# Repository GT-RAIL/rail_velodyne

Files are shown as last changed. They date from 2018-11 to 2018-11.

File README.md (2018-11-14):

# RAIL Velodyne

This rail_velodyne repository includes custom packages required to install, simulate, and use the Velodyne VLP-16 with the Fetch. The drivers which bring up the physical VLP-16 were forked from [here](https://github.com/ros-drivers/velodyne) while the customized launch files to start the Fetch simluations that include the VLP-16 reuse models from [here](https://bitbucket.org/DataspeedInc/velodyne_simulator).

# Dependencies
Fetch packages for simulation. Please see [their site](http://docs.fetchrobotics.com/index.html) for installation instructions.

## Menu
1. [3D printed Mounts](#3d-printed-mounts) Go here to view the mounts for the VLP-16 and battery on Fetch.
2. [Fetch with Velodyne in Simulation](#fetch-with-velodyne-in-simulation) Go here for simulation install.
3. [Fetch with Velodyne on physical hardware](#fetch-with-velodyne-on-physical-hardware) Go here for robot install.
4. [Toggle the Velodyne on the Fetch](#toggle-the-velodyne-on-the-fetch) Go here to enable/disable Velodyne on robot.

## 3D printed Mounts
Mounts for VLP-16 and battery are found in [here](https://github.com/adaruna3/rail_velodyne/tree/master/fetch_velodyne/hardware). Some images of these mounts are below:

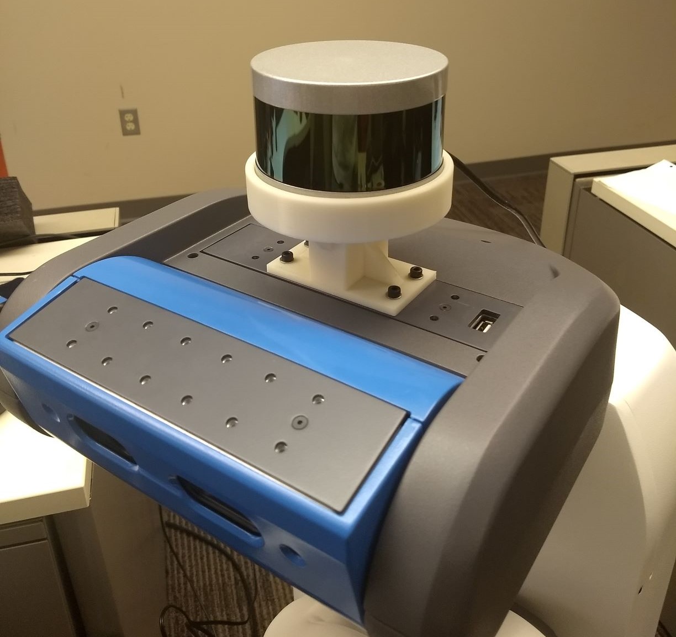
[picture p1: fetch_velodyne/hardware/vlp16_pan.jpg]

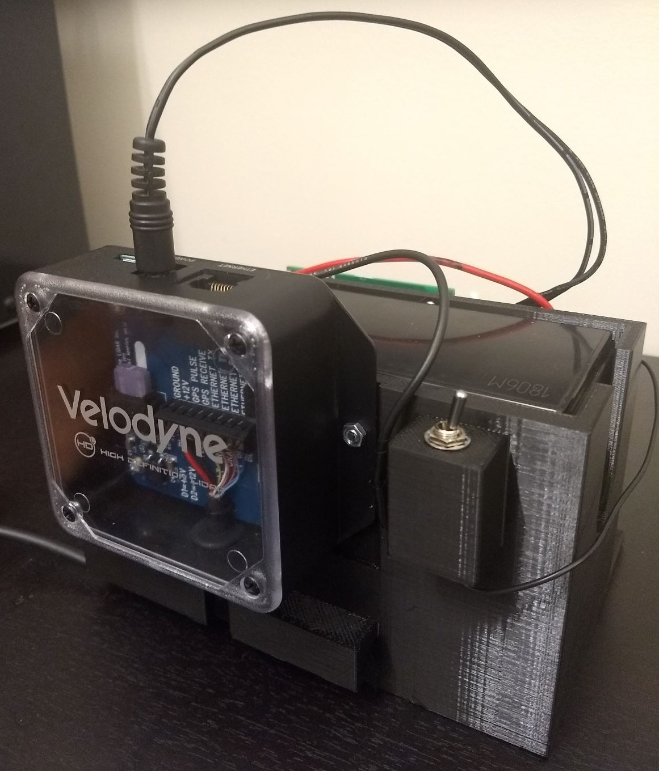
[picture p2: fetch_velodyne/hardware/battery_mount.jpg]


## Fetch with Velodyne in Simulation
This goes through the process of installing and running the simulations for Fetch including the VLP-16.

### Install Fetch / Velodyne Simulator to a PC
1. Begin by installing the Gazebo simulation packages for the VLP-16: `sudo apt-get install ros-indigo-velodyne-simulator`
2. Next clone this repo into a catkin workspace you intend to use.
3. Install dependencies via rosdep: `rosdep install --from-paths src --ignore-src --rosdistro indigo -y`
4. Run `catkin_make` in the catkin workspace to build the pacakges and remember to source the `setup.bash` in the `devel` folder.

### Verify Fetch / Velodyne Simulator Installation
1. Run the simulator via `roslaunch fetch_velodyne playground.launch`. This should begin Gazebo with the Fetch including the VLP-16 on it's pan joint in the defualt playground environment.
2. Check the topics being published via `rostopic list`. There should be a topic called `/velodyne/depth/points`.
3. Visualize the points being published in rviz via `rosrun rviz rviz -f velodyne` using the PointCloud2 rviz pluggin.

## Fetch with Velodyne on physical hardware
This goes through the installation of the VLP-16 and it's drivers into the Fetch. NOTE: To simply use the VLP-16 once it has already been installed (most cases), skip to **Toggle the Velodyne on the Fetch** below.

### Configure Fetch Networking for VLP-16
1. Power the VLP-16 and plug it into Fetch's external Ethernet.
2. Access Fetch via ssh or some other method and modify the `/etc/network/interfaces` file to include the following regarding `eth0` (this will allow the Velodyne to be accessed):
```
auto eth0
iface eth0 inet static
    address 192.168.1.11
    netmask 255.255.255.0
    gateway 192.168.1.1
```
3. Restart Fetch to reset the networking service.

### Verify Fetch Networking Configuration for VLP-16
1. Verify network configuration by running `ifconfig`. The network setting for `eth0` should read similar to `inet addr:192.168.1.11  Bcast:192.168.1.255  Mask:255.255.255.0`
2. Access Fetch via ssh or some other method and open a browser to access the web-server hosted by the VLP-16 at `192.168.1.201`. If networking was set up properly, you should be able to both ping this IP and view the web-server default page *from a web-browser on the Fetch*.

### Install VLP-16 drivers to the Fetch
1. Access Fetch via ssh or some other method and clone this repo into a catkin workspace you intend to use.
2. Access Fetch via ssh or some other method and install dependencies via rosdep for the workspace: `rosdep install --from-paths src --ignore-src --rosdistro indigo -y`
3. Access Fetch via ssh or some other method and run `catkin_make` in the catkin workspace to build the pacakges and remember to source the `setup.bash` in the `devel` folder.

### Verify VLP-16 drivers Installation to the Fetch
1. Access Fetch via ssh or some other method and run `roslaunch velodyne_pointcloud VLP16_points.launch` to start the drivers.
2. Check the topics being published via `rostopic list`. There should be a topic called `/velodyne/depth/points`.
3. Visualize the points being published in rviz via `rosrun rviz rviz -f velodyne` using the PointCloud2 rviz pluggin.

### Configure the Fetch URDF and Startup Services to include the VLP-16
1. This section will be involved, but once properly conifgured the VLP-16 can be toggled by commenting a single line. Begin by locating the startup service that launches all the drivers for the robot. From the Fetch [documentation](http://docs.fetchrobotics.com/computer.html), it should located at `/etc/init/robot.conf`. We will edit this file, but before doing so, save a copy `sudo cp /etc/init/robot.conf /etc/init/robot.conf.bak`.
2. Open the file for editting in vi via `sudo vi /etc/init/robot.conf` Notice this file sources the default ROS `setup.bash` then launches the robot at line 9. Copy this line directly below and modify it to *also* source the workspace where the VLP-16 drivers have been installed as well as launch the robot via a new file we will create called `robot_velodyne.launch`. This should look something like:
```
exec su ros -c ". /opt/ros/indigo/setup.bash && . /PATH_TO_VLP16_DRIVERS/devel/setup.bash && roslaunch /etc/ros/indigo/robot_velodyne.launch --wait"
```
3. Now comment the original line so that instead the line you just wrote gets called. Write the changes and quit vim.
4. Now we will write the file which was just mentioned, `robot_velodyne.launch`. To do this we will use the default file `robot.launch` as a template. Copy this file in the same directory, renaming it accordingly via `sudo cp /etc/ros/indigo/robot.launch /etc/ros/indigo/robot_velodyne.launch`.
5. **Pay attention to the following steps** as *they will differ whether or not the Fetch has been manually calibrated* yet. Open the file in vi via `sudo vi /etc/ros/indigo/robot_velodyne.launch`. If the Fetch *has not been calibrated before*, then modify the line which reads:
```
<!-- URDF -->
<param name="robot_description" textfile="$(find fetch_description)/robots/fetch.urdf" />
```
to
```
<!-- URDF -->
<param name="robot_description" textfile="$(find fetch_velodyne)/robots/fetch_velodyne.urdf" />
```
Otherwise, if the Fetch *has been calibrated before*, it will likely look more like:
```
<!-- URDF -->
<param name="robot_description" textfile="/etc/ros/indigo/CALIBRATION_FILE_NAME.urdf" />
```
in which case you should modify it to

```
<!-- URDF -->
<param name="robot_description" textfile="/etc/ros/indigo/velodyne_CALIBRATION_FILE_NAME.urdf" />
```
6. Before closing this file, we want to add a couple more lines of code to start the VLP-16 drivers. Insert the following code snippet between the `Laser` and `Teleop` drivers to start the Velodyne:
```
<!-- Velodyne -->
<include file="$(find velodyne_pointcloud)/launch/VLP16_points.launch"/>
```
An example file for the case where the Fetch has not be calibrated is in the `launch` folder of the `fetch_velodyne` package titled `robot_velodyne.launch`.

7. Write the changes to the file and quit vi.

8. If the Fetch *has not been calibrated before* skip to configuration verification. Otherwise, if the Fetch *has been calibrated before* please follow this step.  In the step 8, we modified the `robot_velodyne.launch` to reference a URDF which does not exist, therefore we need to create it. To do this, we want to re-use the current calibration which was refernced in step 7. To do this we copy the current calibration's URDF as a template and rename it accordingly via a command *similar* to `sudo cp /etc/ros/indigo/CALIBRATION_FILE_NAME.urdf /etc/ros/indigo/velodyne_CALIBRATION_FILE_NAME.urdf`. Now open that file in an editor with sudo priveleges and add the following code snippet before writing the changes and closing it (from lines 159-223 of the `fetch_velodyne.urdf` inside the `fetch_velodyne` package):
```
<!-- Velodyne VLP-16 Mount -->
  <link name="velodyne_base_link">
    <inertial> <!-- calculated via SolidWorks output -->
      <origin rpy="0 0 0" xyz="0 0 0.0437" />
      <mass value="0.166" />
      <inertia ixx="0.0002" ixy="0.0" ixz="0.0" iyy="0.0002" iyz="0.0" izz="0.0002" />
    </inertial>
    <visual>
      <origin rpy="0 0 0" xyz="0 0 -0.0275" />
      <geometry> <!-- mesh to be added... -->
        <cylinder length="0.055" radius="0.0515"/>
      </geometry>
      <material name="grey">
        <color rgba="0.3 0.3 0.3 1" />
      </material>
    </visual>
    <collision>
      <origin rpy="0 0 0" xyz="0 0 -0.0275" />
      <geometry> <!-- mesh to be added... -->
        <cylinder length="0.055" radius="0.0515"/>
      </geometry>
    </collision>
  </link> 
  <joint name="velodyne_mount_joint" type="fixed">
    <origin rpy="0 0 0" xyz="0.046065 0.000065 0.13735" />
    <parent link="head_pan_link" />
    <child link="velodyne_base_link" />
  </joint>
  <!-- Velodyne VLP-16 -->
  <link name="velodyne_link">
    <inertial>
      <mass value="0.1"/>
      <origin xyz="0 0 -0.0377" />
      <inertia ixx="0.1" ixy="0" ixz="0" iyy="0.1" iyz="0" izz="0.1"/>
    </inertial>
    <visual>
      <origin xyz="0 0 -0.0377" />
      <geometry>
        <mesh filename="package://velodyne_description/meshes/VLP16_base_1.dae" />
      </geometry>
    </visual>
    <visual>
      <origin xyz="0 0 -0.0377" />
      <geometry>
        <mesh filename="package://velodyne_description/meshes/VLP16_base_2.dae" />
      </geometry>
    </visual>
    <visual>
      <origin xyz="0 0 -0.0377" />
      <geometry>
        <mesh filename="package://velodyne_description/meshes/VLP16_scan.dae" />
      </geometry>
    </visual>
    <collision>
      <origin rpy="0 0 0" xyz="0 0 -0.00185"/>
      <geometry>
        <cylinder radius="0.0516" length="0.0717"/>
      </geometry>
    </collision>
  </link>
  <joint name="velodyne_joint" type="fixed">
    <origin xyz="0 0 0.0377" rpy="0 0 0" />
    <parent link="velodyne_base_link"/>
    <child link="velodyne_link"/>
  </joint>
```
### Verify the Fetch URDF and Startup Services Configuration to include the VLP-16
1. Restart the Fetch with the VLP-16 plugged into the Fetch via ethernet and powered on.
2. Access Fetch via ssh or some other method and run `rostopic list`. Now the topic `/velodyne/depth/points` should be getting published by default.
3. Run rviz via `rosrun rviz rviz` and add the robot model pluggin as needed to view the robot URDF. It should now include the VLP-16.
4. Visualize the points being published in rviz using the PointCloud2 rviz pluggin.
5. Installation is complete.

## Toggle the Velodyne on the Fetch
### Enable the VLP-16
1. Run `sudo vi /etc/init/robot.conf`
2. Uncomment the `exec` line that contains the word `velodyne`
3. Comment the `exec` line that does not contain the word `velodyne`

### Disable the VLP-16
1. Run `sudo vi /etc/init/robot.conf`
2. Comment the `exec` line that contains the word `velodyne`
3. Unomment the `exec` line that does not contain the word `velodyne`

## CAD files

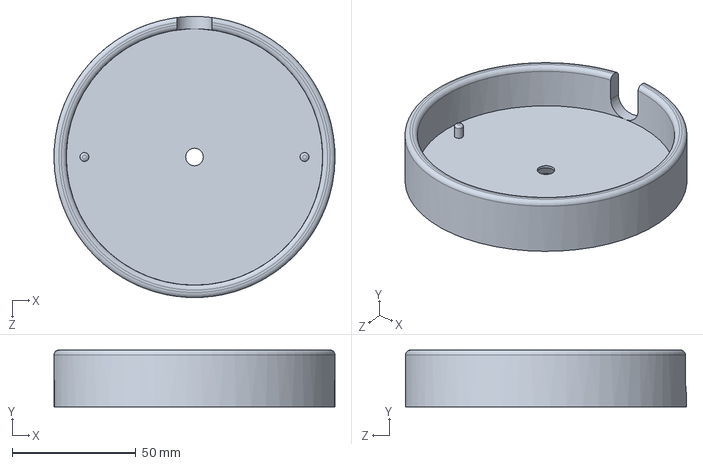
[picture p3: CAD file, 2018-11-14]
fetch_velodyne/hardware/vlp16_mount_base.SLDPRT
113.5 x 23.0 x 113.5 mm

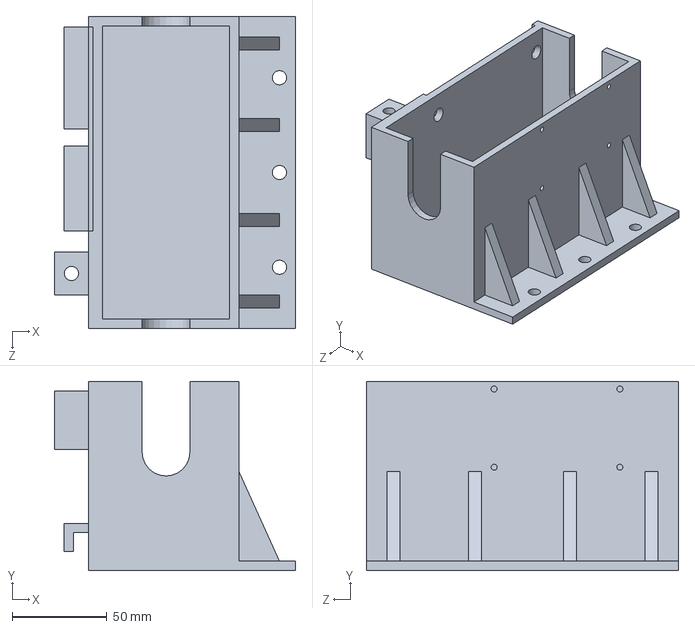
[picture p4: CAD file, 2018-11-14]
fetch_velodyne/hardware/battery_mount.SLDPRT
127.5 x 100.0 x 165.0 mm

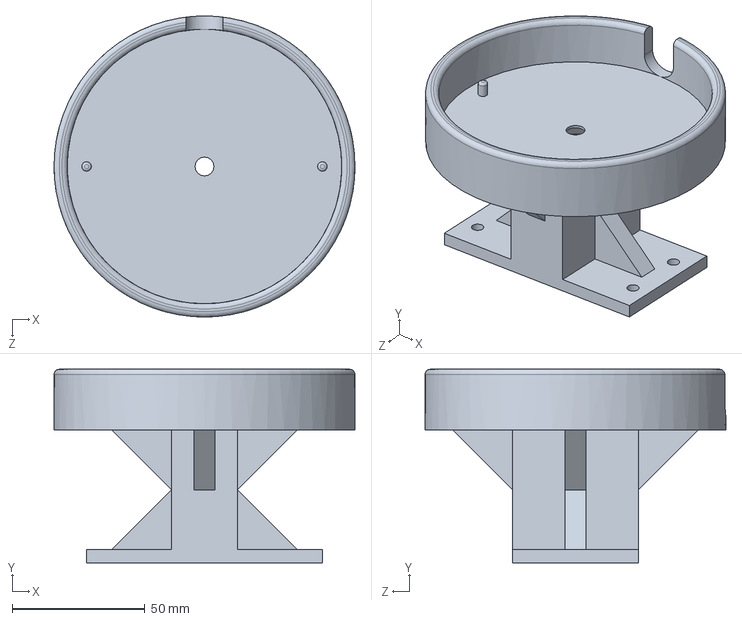
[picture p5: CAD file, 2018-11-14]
fetch_velodyne/hardware/vlp16_mount_pan.SLDPRT
113.5 x 73.0 x 113.5 mm

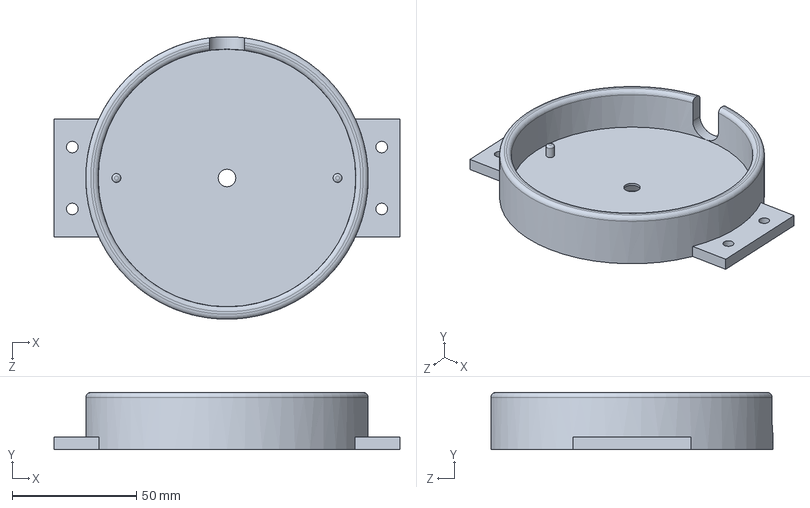
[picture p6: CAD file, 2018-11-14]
fetch_velodyne/hardware/vlp16_mount_tilt.SLDPRT
139.0 x 23.0 x 113.5 mm

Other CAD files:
fetch_velodyne/hardware/battery_mount.STL
fetch_velodyne/hardware/vlp16_mount_pan.STL
fetch_velodyne/hardware/vlp16_mount_tilt.STL

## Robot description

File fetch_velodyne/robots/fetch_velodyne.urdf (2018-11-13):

<robot name="fetch">
  <link name="base_link">
    <inertial>
      <origin rpy="0 0 0" xyz="-0.0036 0.0 0.0014" />
      <mass value="70.1294" />
      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
    </inertial>
    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
  </link>
  <link name="r_wheel_link">
    <inertial>
      <origin rpy="0 0 0" xyz="0 0 0" />
      <mass value="4.3542" />
      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
    </inertial>
    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
  </link>
  <joint name="r_wheel_joint" type="continuous">
    <origin rpy="-6.123E-17 0 0" xyz="0.0012914 -0.18738 0.055325" />
    <parent link="base_link" />
    <child link="r_wheel_link" />
    <axis xyz="0 1 0" />
  <limit effort="8.85" velocity="17.4" /></joint>
  <link name="l_wheel_link">
    <inertial>
      <origin rpy="0 0 0" xyz="0 0 0" />
      <mass value="4.3542" />
      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
    </inertial>
    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
  </link>
  <joint name="l_wheel_joint" type="continuous">
    <origin rpy="-6.123E-17 0 0" xyz="0.0012914 0.18738 0.055325" />
    <parent link="base_link" />
    <child link="l_wheel_link" />
    <axis xyz="0 1 0" />
  <limit effort="8.85" velocity="17.4" /></joint>
  <link name="torso_lift_link">
    <inertial>
      <origin rpy="0 0 0" xyz="-0.0013 -0.0009 0.2935" />
      <mass value="10.7796" />
      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
    </inertial>
    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
  </link>
  <joint name="torso_lift_joint" type="prismatic">
    <origin rpy="-6.123E-17 0 0" xyz="-0.086875 0 0.37743" />
    <parent link="base_link" />
    <child link="torso_lift_link" />
    <axis xyz="0 0 1" />
    <limit effort="450.0" lower="0" upper="0.38615" velocity="0.1" />
  <dynamics damping="100.0" /></joint>
  <link name="head_pan_link">
    <inertial>
      <origin rpy="0 0 0" xyz="0.0321 0.0161 0.0390" />
      <mass value="2.2556" />
      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
    </inertial>
    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
  </link>
  <joint name="head_pan_joint" type="revolute">
    <origin rpy="0 0 0" xyz="0.053125 0 0.603001417713939" />
    <parent link="torso_lift_link" />
    <child link="head_pan_link" />
    <axis xyz="0 0 1" />
  <limit effort="0.32" lower="-1.57" upper="1.57" velocity="1.57" /></joint>
  <link name="head_tilt_link">
    <inertial>
      <origin rpy="0 0 0" xyz="0.0081 0.0025 0.0113" />
      <mass value="0.9087" />
      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
    </inertial>
    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
  </link>
  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
  <link name="velodyne_base_link">
    <inertial> 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
      <origin rpy="0 0 0" xyz="0 0 0.0437" />
      <mass value="0.166" />
      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
    </inertial>
    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
  </link> 
  <joint name="velodyne_mount_joint" type="fixed">
    <origin rpy="0 0 0" xyz="0.046065 0.000065 0.13735" />
    <parent link="head_pan_link" />
    <child link="velodyne_base_link" />
  </joint>
  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
  <link name="velodyne_link">
    <inertial>
      <mass value="0.1"/>
      <origin xyz="0 0 -0.0377" />
      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
    </inertial>
    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
  </link>
  <joint name="velodyne_joint" type="fixed">
    <origin xyz="0 0 0.0377" rpy="0 0 0" />
    <parent link="velodyne_base_link"/>
    <child link="velodyne_link"/>
  </joint> 
  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
  <joint name="head_tilt_joint" type="revolute">
    <origin rpy="0 0 0" xyz="0.14253 0 0.057999" />
    <parent link="head_pan_link" />
    <child link="head_tilt_link" />
    <axis xyz="0 1 0" />
    <limit effort="0.68" lower="-0.76" upper="1.45" velocity="1.57" />
  </joint>
  <link name="shoulder_pan_link">
    <inertial>
      <origin rpy="0 0 0" xyz="0.0927 -0.0056 0.0564" />
      <mass value="2.5587" />
      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
    </inertial>
    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
  </link>
  <joint name="shoulder_pan_joint" type="revolute">
    <origin rpy="0 0 0" xyz="0.119525 0 0.34858" />
    <parent link="torso_lift_link" />
    <child link="shoulder_pan_link" />
    <axis xyz="0 0 1" />
    <dynamics damping="1.0" />
    <limit effort="33.82" lower="-1.6056" upper="1.6056" velocity="1.256" />
  </joint>
  <link name="shoulder_lift_link">
    <inertial>
      <origin rpy="0 0 0" xyz="0.1432 0.0072 -0.0001" />
      <mass value="2.6615" />
      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
    </inertial>
    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
  </link>
  <joint name="shoulder_lift_joint" type="revolute">
    <origin rpy="0 0 0" xyz="0.117 0 0.0599999999999999" />
    <parent link="shoulder_pan_link" />
    <child link="shoulder_lift_link" />
    <axis xyz="0 1 0" />
    <dynamics damping="1.0" />
    <limit effort="131.76" lower="-1.221" upper="1.518" velocity="1.454" />
  </joint>
  <link name="upperarm_roll_link">
    <inertial>
      <origin rpy="0 0 0" xyz="0.1165 0.0014 0.0000" />
      <mass value="2.3311" />
      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
    </inertial>
    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
  </link>
  <joint name="upperarm_roll_joint" type="continuous">
    <origin rpy="0 0 0" xyz="0.219 0 0" />
    <parent link="shoulder_lift_link" />
    <child link="upperarm_roll_link" />
    <axis xyz="1 0 0" />
    <dynamics damping="5.0" />
    <limit effort="76.94" velocity="1.571" />
  </joint>
  <link name="elbow_flex_link">
    <inertial>
      <origin rpy="0 0 0" xyz="0.1279 0.0073 0.0000" />
      <mass value="2.1299" />
      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
    </inertial>
    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
  </link>
  <joint name="elbow_flex_joint" type="revolute">
    <origin rpy="0 0 0" xyz="0.133 0 0" />
    <parent link="upperarm_roll_link" />
    <child link="elbow_flex_link" />
    <axis xyz="0 1 0" />
    <dynamics damping="1.0" />
    <limit effort="66.18" lower="-2.251" upper="2.251" velocity="1.521" />
  </joint>
  <link name="forearm_roll_link">
    <inertial>
      <origin rpy="0 0 0" xyz="0.1097 -0.0266 0.0000" />
      <mass value="1.6563" />
      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
    </inertial>
    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
  </link>
  <joint name="forearm_roll_joint" type="continuous">
    <origin rpy="0 0 0" xyz="0.197 0 0" />
    <parent link="elbow_flex_link" />
    <child link="forearm_roll_link" />
    <axis xyz="1 0 0" />
    <dynamics damping="5.0" />
    <limit effort="29.35" velocity="1.571" />
  </joint>
  <link name="wrist_flex_link">
    <inertial>
      <origin rpy="0 0 0" xyz="0.0882 0.0009 -0.0001" />
      <mass value="1.725" />
      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
    </inertial>
    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
  </link>
  <joint name="wrist_flex_joint" type="revolute">
    <origin rpy="0 0 0" xyz="0.1245 0 0" />
    <parent link="forearm_roll_link" />
    <child link="wrist_flex_link" />
    <axis xyz="0 1 0" />
    <dynamics damping="1.0" />
    <limit effort="25.7" lower="-2.16" upper="2.16" velocity="2.268" />
  </joint>
  <link name="wrist_roll_link">
    <inertial>
      <origin rpy="0 0 0" xyz="0.0095 0.0004 -0.0002" />
      <mass value="0.1354" />
      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
    </inertial>
    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
  </link>
  <joint name="wrist_roll_joint" type="continuous">
    <origin rpy="0 0 0" xyz="0.1385 0 0" />
    <parent link="wrist_flex_link" />
    <child link="wrist_roll_link" />
    <axis xyz="1 0 0" />
    <limit effort="7.36" velocity="2.268" />
    <dynamics damping="5.0" />
  </joint>
  <link name="gripper_link">
    <inertial>
      <origin rpy="0 0 0" xyz="-0.0900 -0.0001 -0.0017" />
      <mass value="1.5175" />
      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
    </inertial>
    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
  </link>
  <joint name="gripper_axis" type="fixed">
    <origin rpy="0 0 0" xyz="0.16645 0 0" />
    <parent link="wrist_roll_link" />
    <child link="gripper_link" />
    <axis xyz="0 1 0" />
  </joint>
  <link name="r_gripper_finger_link">
    <inertial>
      <origin rpy="0 0 0" xyz="-0.01 0 0" />
      <mass value="0.0798" />
      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
    </inertial>
    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
  </link>
  <joint name="r_gripper_finger_joint" type="prismatic">
    <origin rpy="0 0 0" xyz="0 0.015425 0" />
    <parent link="gripper_link" />
    <child link="r_gripper_finger_link" />
    <axis xyz="0 1 0" />
  <limit effort="60" lower="0.0" upper="0.05" velocity="0.05" /><dynamics damping="100.0" /></joint>
  <link name="l_gripper_finger_link">
    <inertial>
      <origin rpy="0 0 0" xyz="-0.01 0 0" />
      <mass value="0.0798" />
      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
    </inertial>
    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
  </link>
  <joint name="l_gripper_finger_joint" type="prismatic">
    <origin rpy="0 0 0" xyz="0 -0.015425 0" />
    <parent link="gripper_link" />
    <child link="l_gripper_finger_link" />
    <axis xyz="0 -1 0" />
  <limit effort="60" lower="0.0" upper="0.05" velocity="0.05" /><dynamics damping="100.0" /></joint>
  <link name="bellows_link">
    <inertial>
      <origin rpy="0 0 0" xyz="0.0191320000286228 -1.67219873481315E-16 -0.134861625443387" />
      <mass value="0.169374038216602" />
      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

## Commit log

2018-11-08 integrated simulation and drivers
    [fetch_velodyne.gazebo.xacro]
2018-11-13 changes to xacro and urdf for physical robot
    [fetch_velodyne.gazebo.xacro, fetch_velodyne.urdf]
2018-11-13 made urdf and xacro simpler
    [VLP-16.urdf.xacro, fetch_velodyne.gazebo.xacro, fetch_velodyne.urdf]
2018-11-14 added hardware STL and SLDPRT
    [battery_mount.SLDPRT, battery_mount.STL, vlp16_mount_base.SLDPRT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]
